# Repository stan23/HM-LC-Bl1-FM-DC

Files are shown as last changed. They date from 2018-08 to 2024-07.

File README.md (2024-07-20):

# HM-LC-Bl1-FM-DC          
Nachbau HM-LC-Bl1-FM Rollladenaktor für Gleichstrommotoren (z.B. Plissee)

Er verhält sich wie ein Rolloaktor, treibt aber einen 12/24 V Gleichstrommotor. Dieser wird je nach Fahrtrichtung umgepolt.

Dies basiert auf der hervorragenden Arbeit von [pa-pa](https://github.com/pa-pa/AskSinPP),  [Jérôme](https://github.com/jp112sdl/Beispiel_AskSinPP) und micha68.

[Link zur neueren Version der Platine](https://github.com/stan23/myPCBs/tree/master/HM-LC-Bl1-FM-DC)

## Hardware

### Bauteile

#### Reichelt

[Bestellliste](https://www.reichelt.de/my/1495010)

Bauteil                  | Bestellnummer   | Anzahl | Kommentar
------------------------ | --------------- | ------ | ---------
C6                       | X5R-G0603 10/6  |   1    | -
C1, C2, C3, C8, C21, C22 | X7R-G0603 100N  |   6    | -
C7                       | TAJ 3528 3,3/35 |   1    |  -
R22, R24                 | RND 0603 1 47   |   1    | -
R2                       | RND 0603 1 1,5K |   2    | -
R11, R12                 | RND 0603 1 2,7K |   2    | -
R1, R21, R23             | RND 0603 1 10K  |   3    | -
D1                       | SLO SMD-Y0603-0 |   1    | -
D2, D11, D12             | 1N 4148 WS      |   3    | -
Q1, Q2                   | BC 817 NXP      |   2    | -
U1                       | ATMEGA 328P-AU  |   1    | -
U3                       | SIM1-2403 SIL4  |   1    | für 24 V
U3                       | SIM1-1203 SIL4  |   1    | alternativ für 12 V
K1, K2                   | G6S-2 24V       |   2    | für 24 V
K1, K2                   | G6S-2 12V       |   2    | alternativ für 12 V
X1                       | WAGO 250-204    |   1    | -
X2                       | WAGO 250-404    |   1    | siehe [Issue #1](https://github.com/stan23/HM-LC-Bl1-FM-DC/issues/1)
Verbinder zu U2          | SL 1X20G 2,00   |   1    | -
Verbinder zu U2          | MPE 156-1-032   |   1    | optional

#### Sonstiges

Bauteil | Bestellnummer            | Anzahl | Kommentar
------- | ------------------------ | ------ | ---------
U2      | CC1101 Funkmodul 868MHz  |   1    | z.B. [eBay](https://www.ebay.de/itm/272455136087)

### Programmieradapter
- 1x ISP (um den Bootloader zu brennen)
- 1x FTDI Adapter (falls nicht schon vorhanden, gibts bei [Amazon](https://www.amazon.de/FT232RL-FTDI-USB-auf-TTL-Serienadapter-Arduino/dp/B00HSXDGOE))

## Software

### Fuses

Low:  0xE2
High: 0xD2
Ext:  0xFF

### Bootloader

Aus der Arduino IDE, für ATmega328P, 3,3 V, 8 MHz

### Firmware

https://github.com/pa-pa/AskSinPP/tree/master/examples/HM-LC-Bl1-FM

## Bilder

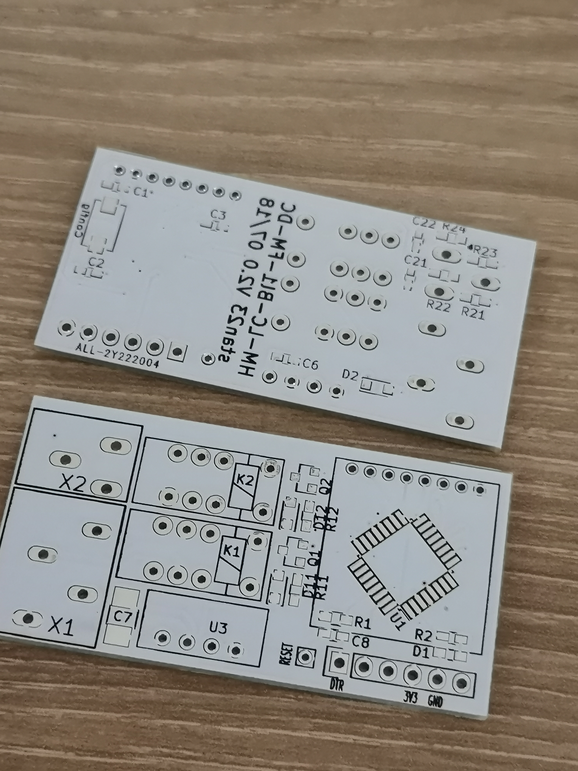
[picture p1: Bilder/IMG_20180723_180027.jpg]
nackte Platine

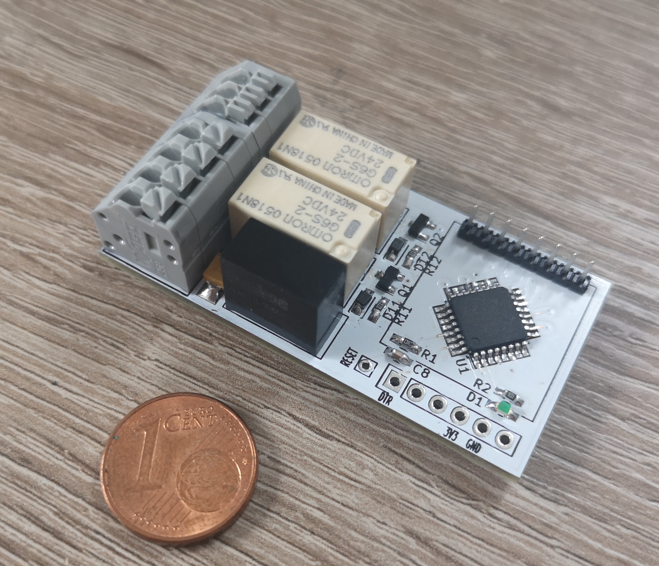
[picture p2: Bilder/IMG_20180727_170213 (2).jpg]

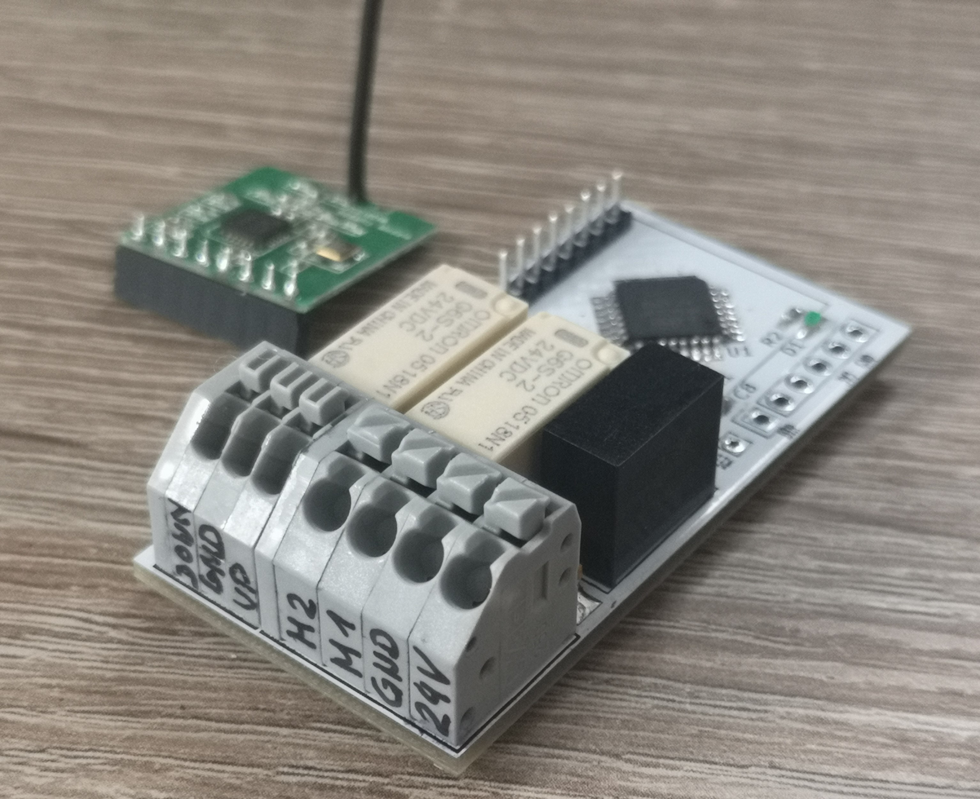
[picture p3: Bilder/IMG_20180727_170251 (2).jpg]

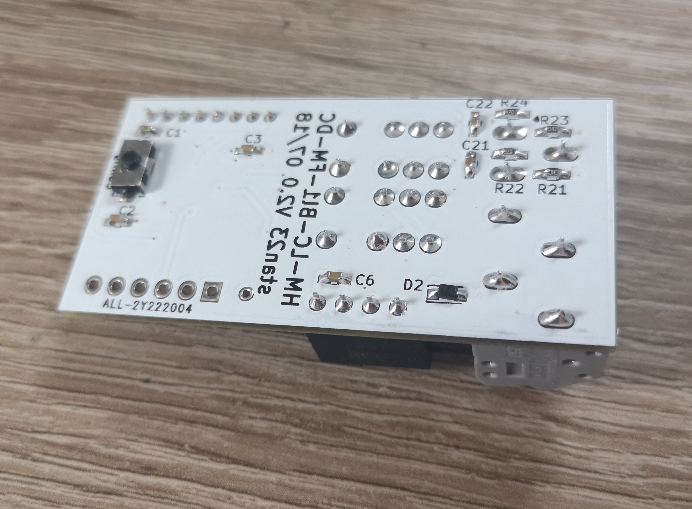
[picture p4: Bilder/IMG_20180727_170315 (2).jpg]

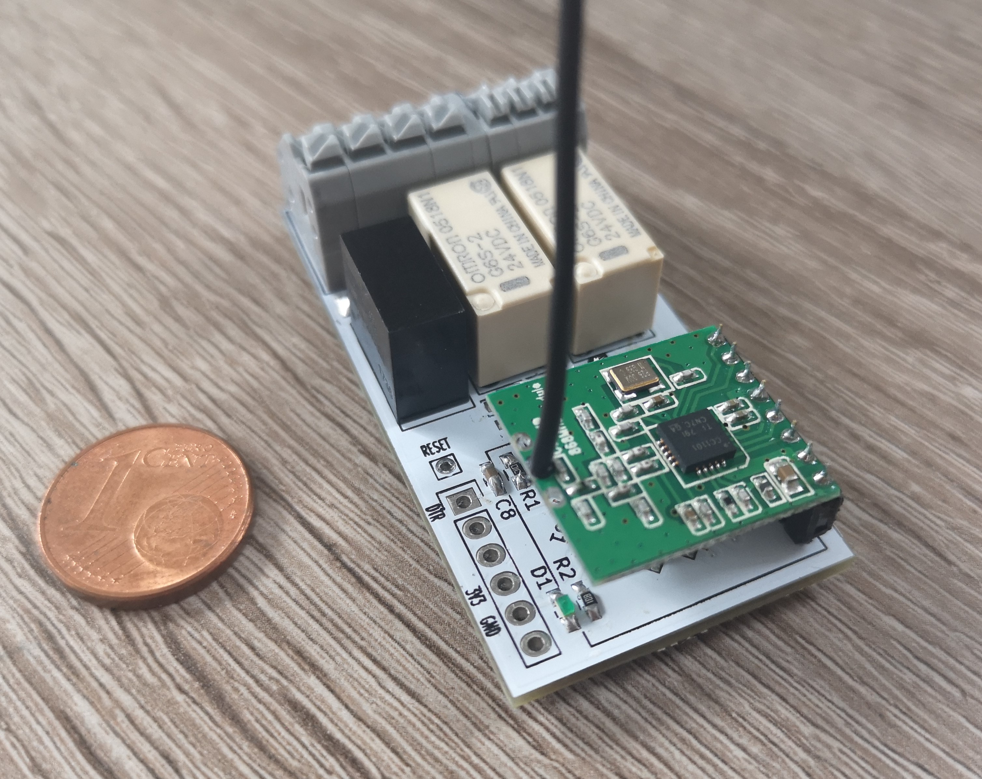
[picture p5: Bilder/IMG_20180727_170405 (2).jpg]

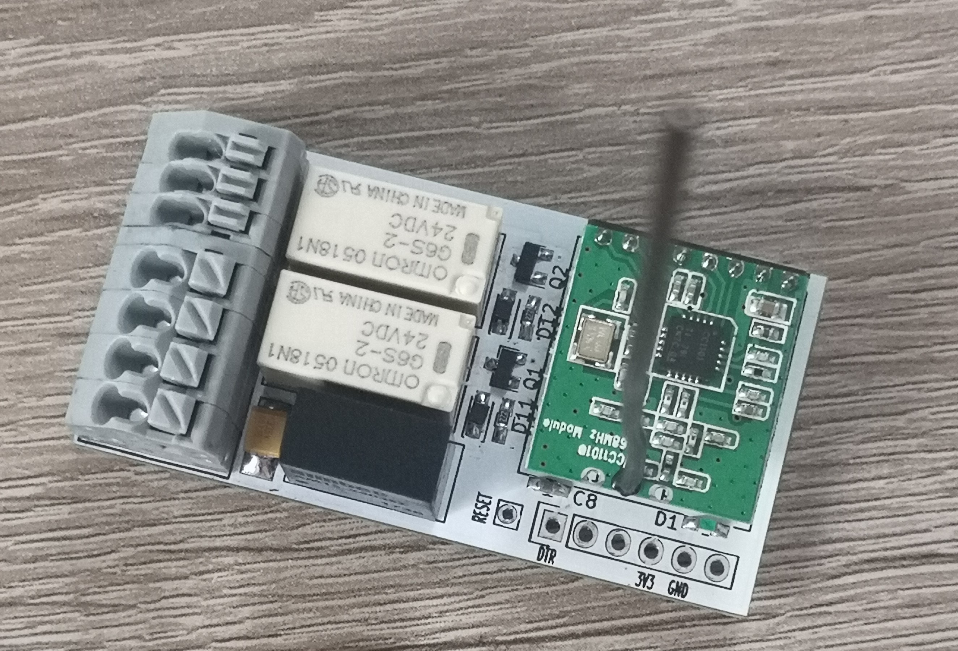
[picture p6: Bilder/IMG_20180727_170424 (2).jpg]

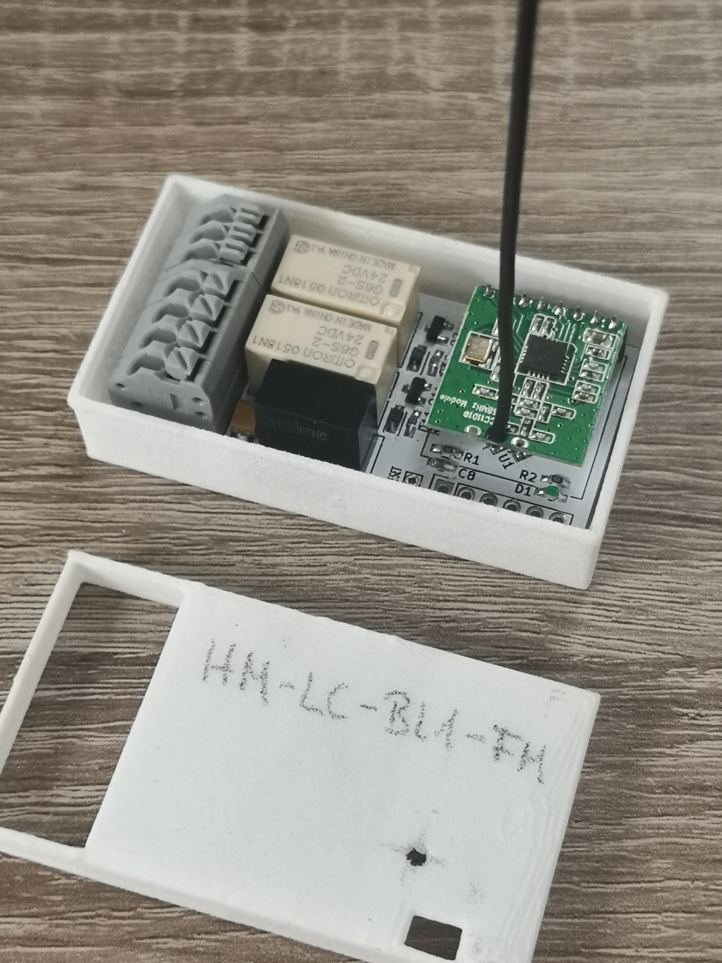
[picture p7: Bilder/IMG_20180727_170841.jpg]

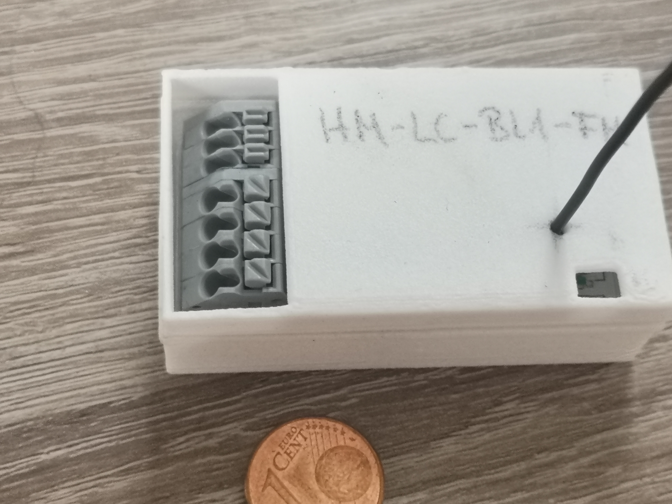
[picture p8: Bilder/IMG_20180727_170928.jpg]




Dieses Werk ist lizenziert unter einer [Creative Commons Namensnennung - Nicht-kommerziell - Weitergabe unter gleichen Bedingungen 4.0 International Lizenz](http://creativecommons.org/licenses/by-nc-sa/4.0/).

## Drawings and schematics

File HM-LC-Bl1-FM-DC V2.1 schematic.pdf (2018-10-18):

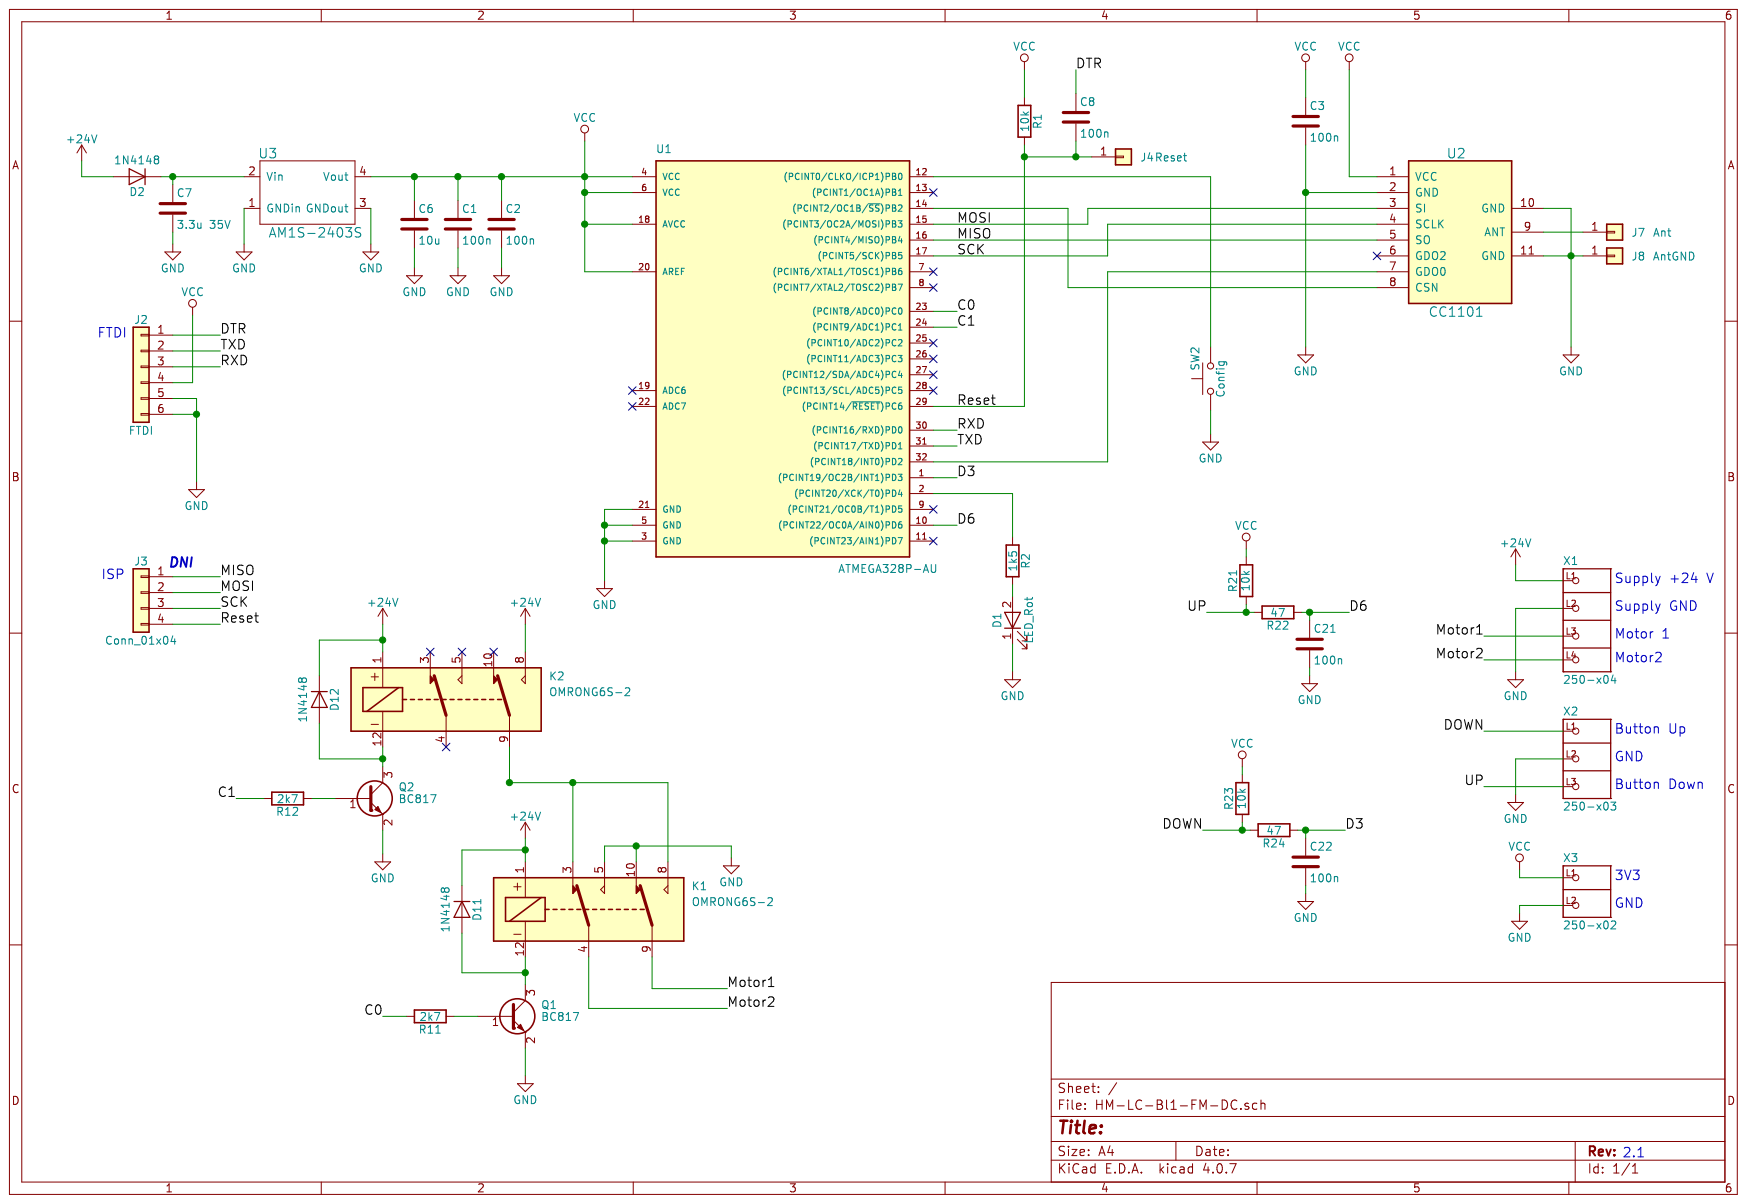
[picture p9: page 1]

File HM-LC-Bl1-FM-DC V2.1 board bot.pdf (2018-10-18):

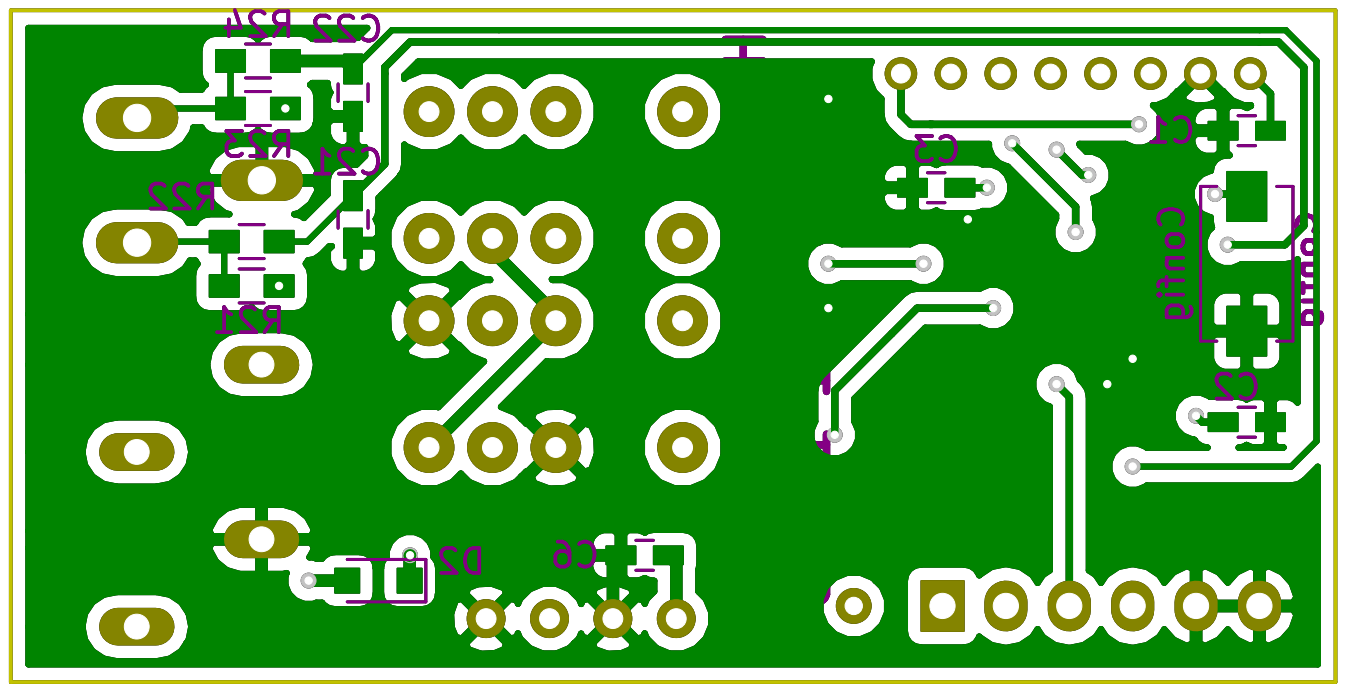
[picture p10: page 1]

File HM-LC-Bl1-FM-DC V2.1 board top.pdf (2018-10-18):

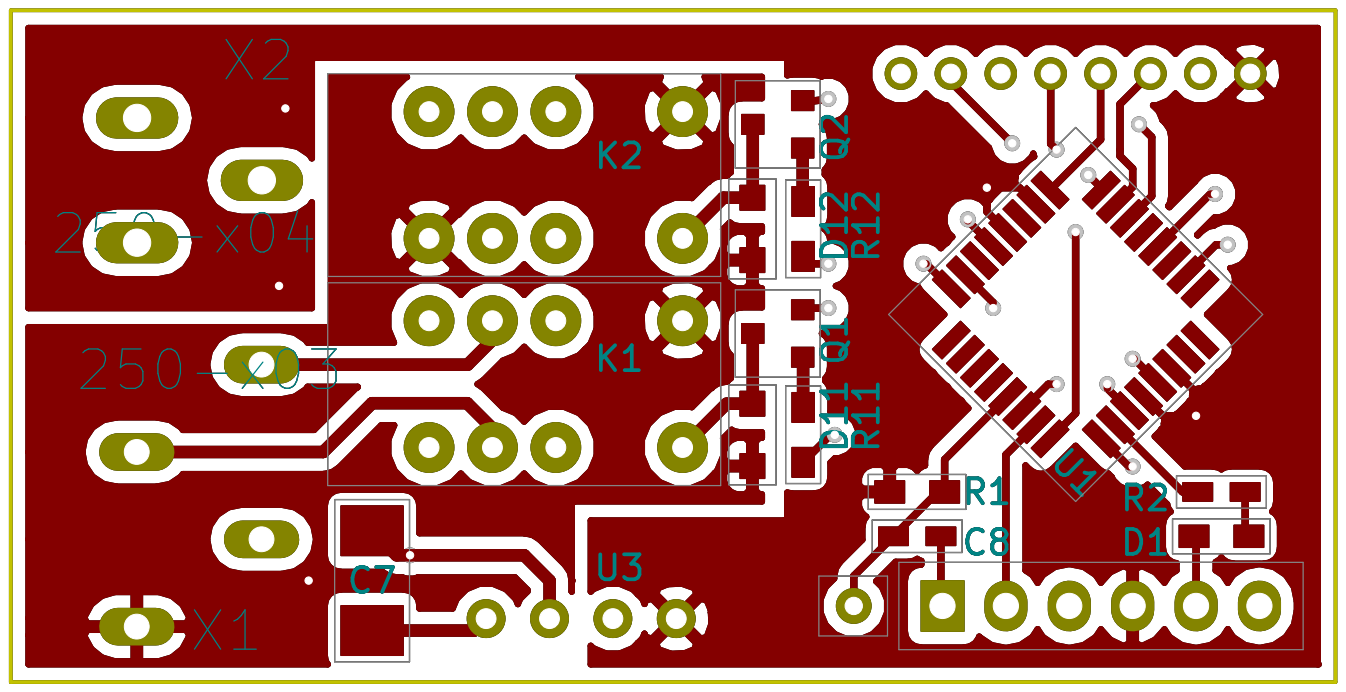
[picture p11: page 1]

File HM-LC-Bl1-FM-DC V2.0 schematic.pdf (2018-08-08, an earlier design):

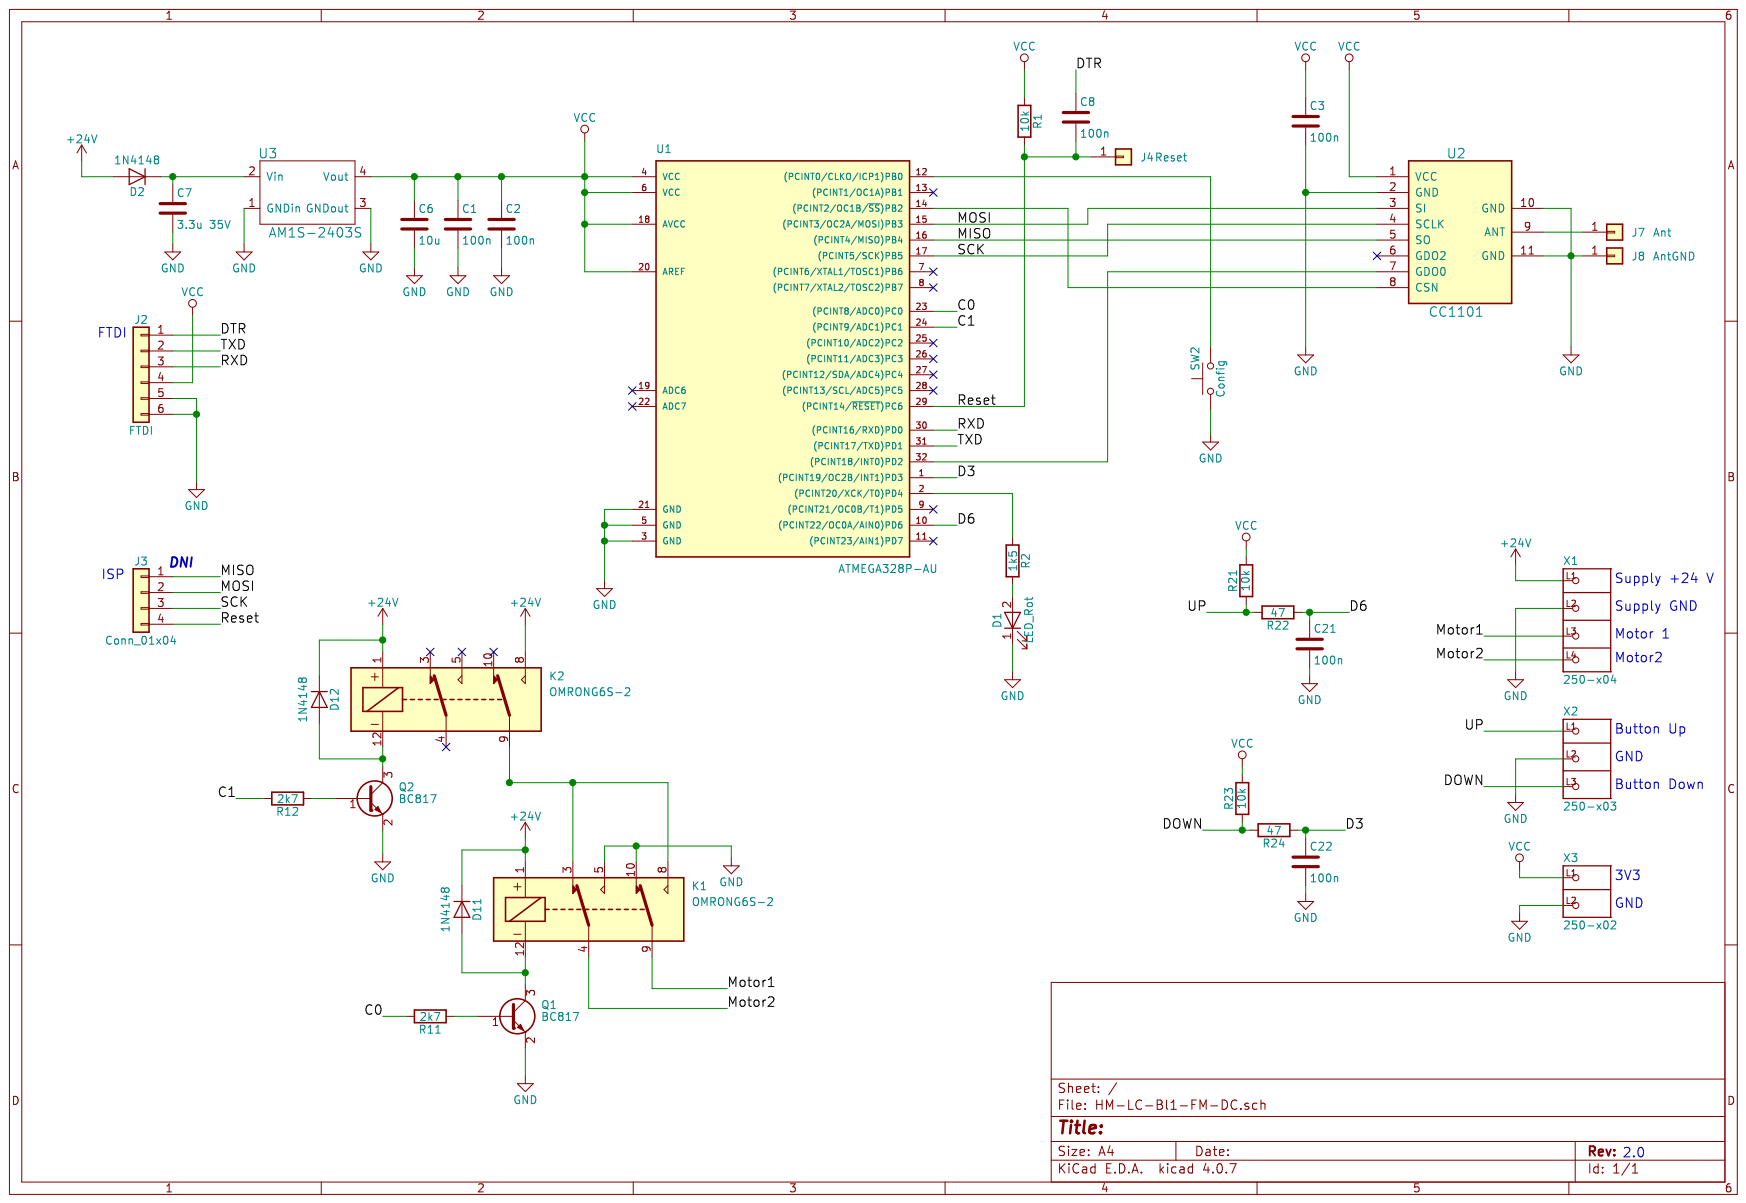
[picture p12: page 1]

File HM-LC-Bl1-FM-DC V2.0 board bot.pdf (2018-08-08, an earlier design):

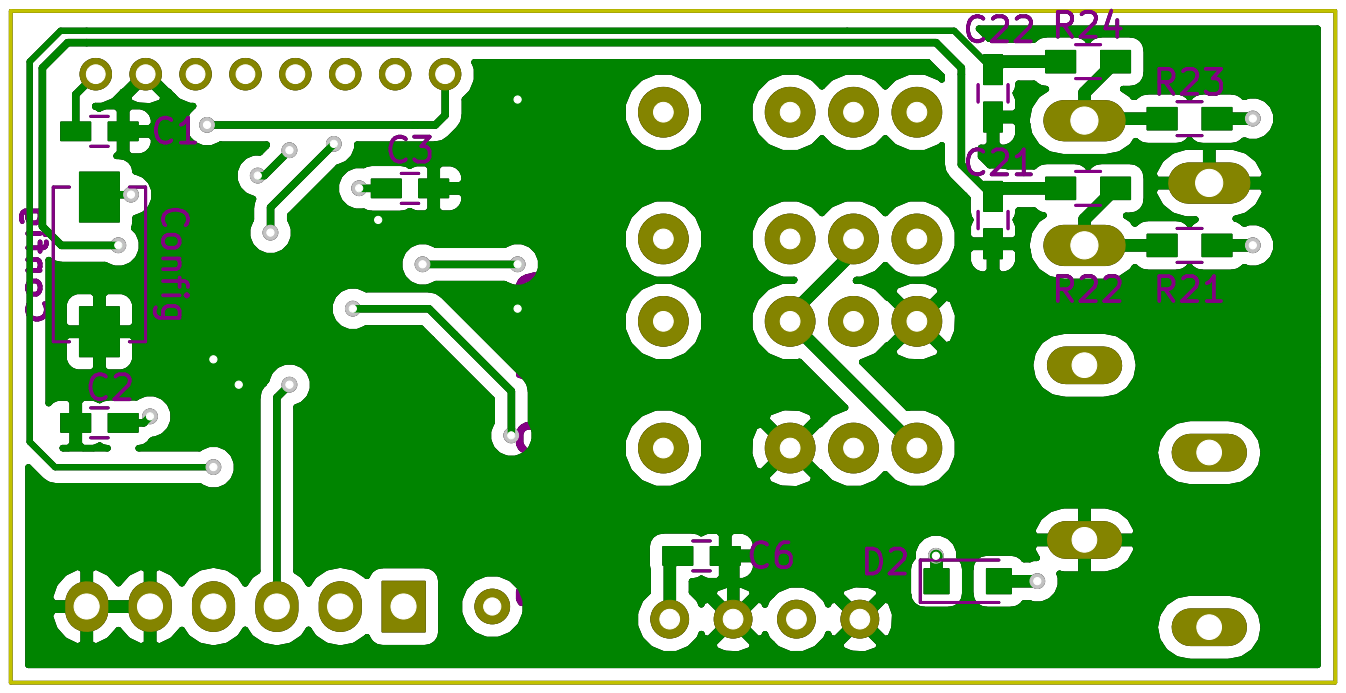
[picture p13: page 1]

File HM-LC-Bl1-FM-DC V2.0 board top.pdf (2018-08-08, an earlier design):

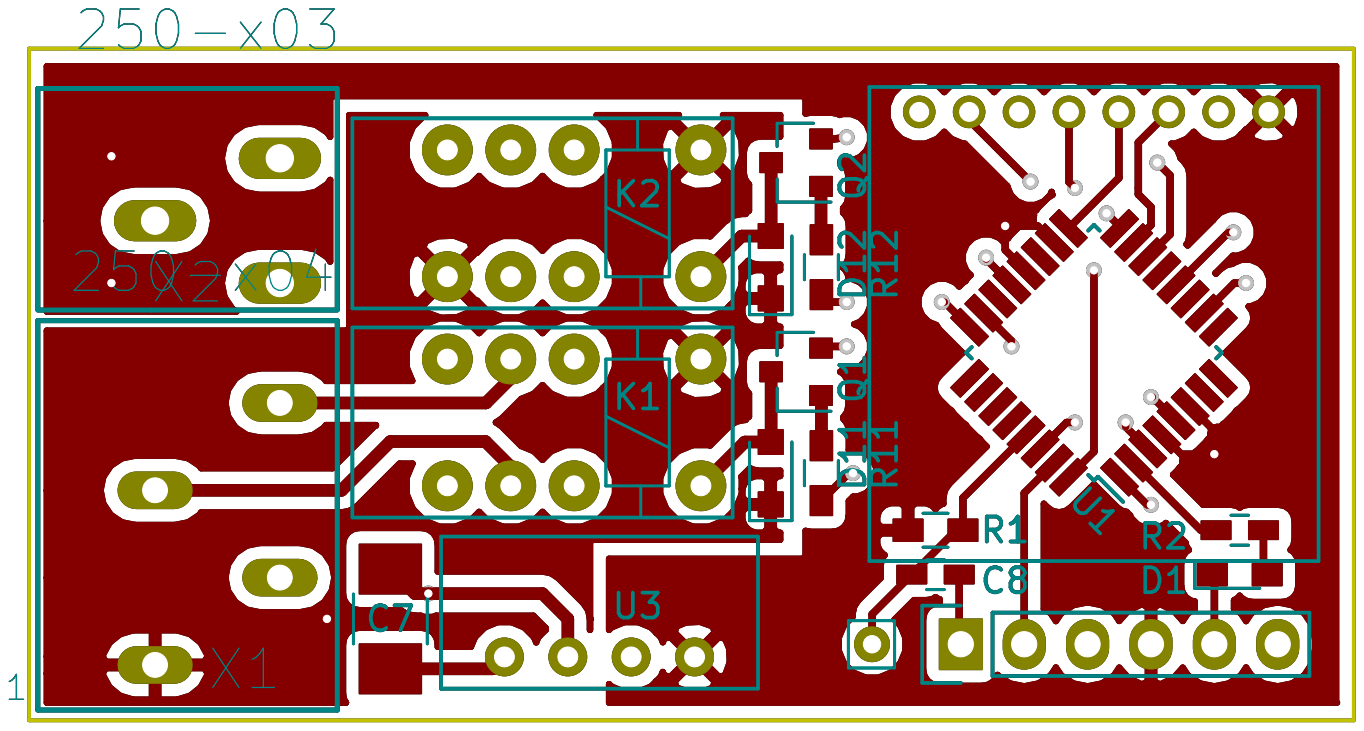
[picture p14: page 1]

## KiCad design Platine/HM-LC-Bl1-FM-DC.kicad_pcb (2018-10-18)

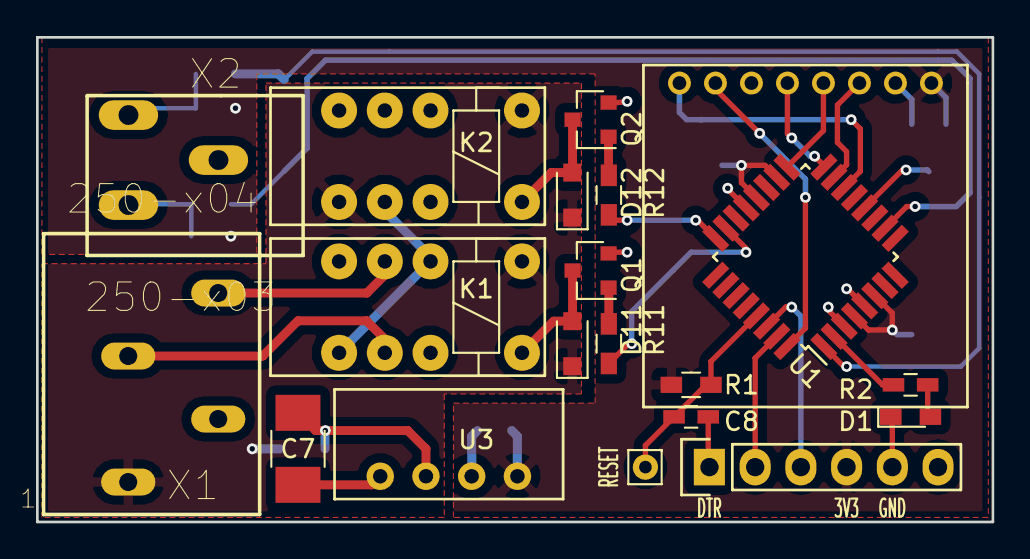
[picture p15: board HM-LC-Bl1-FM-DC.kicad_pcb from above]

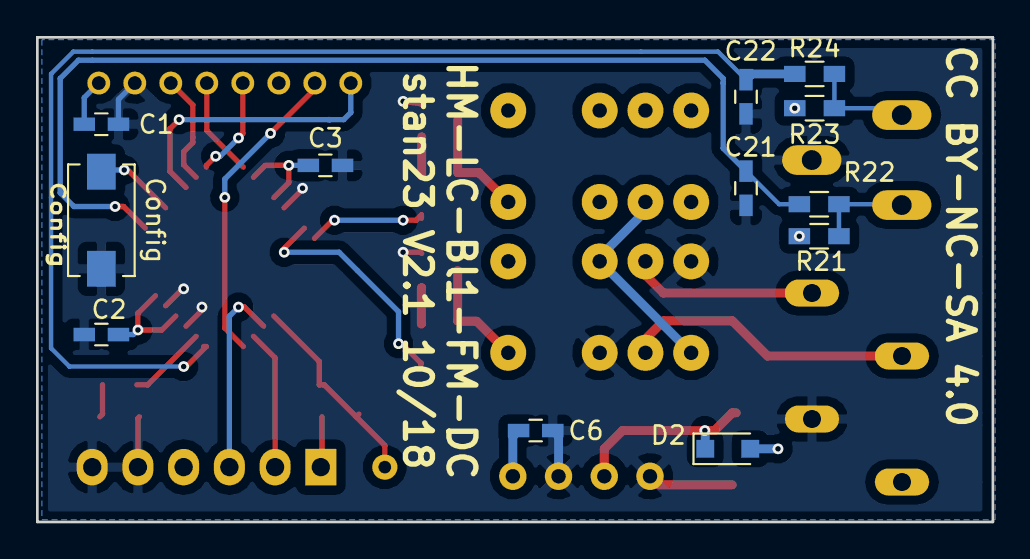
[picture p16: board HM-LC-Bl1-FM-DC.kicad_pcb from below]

Board: 2 copper layers, 53.1 x 26.9 mm, 32 parts (12 on the bottom side), 29 nets.

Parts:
C1, C2, C3, C8, C21, C22: 100n; C_0603_HandSoldering
C6: 10u; C_0603_HandSoldering
C7: 3.3u 35V; C_1210_HandSoldering
D1: LED_Rot; LED_0603_HandSoldering
D2, D11, D12: 1N4148; D_SOD-323_HandSoldering
J2: FTDI; Pin_Header_Straight_1x06
J4: Reset; Pin_d0.7mm_L6.5mm_W1.8mm_FlatFork
K1, K2: OMRONG6S-2; Relay_Omron_G6S-2
Q1, Q2: BC817; SOT-23
R1, R21, R23: 10k; R_0603_HandSoldering
R2: 1k5; C_0603_HandSoldering
R11, R12: 2k7; R_0603_HandSoldering
R22, R24: 47; R_0603_HandSoldering
SW2: Config; SW_SPST_EVQPE1
U1: ATMEGA328P-AU; TQFP-32_7x7mm_Pitch0.8mm
U2: CC1101; CC1101_Module
U3: AM1S-2403S; SIL-4
X1: 250-x04; P-250-204
X2: 250-x03; P-250-403

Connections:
+24V: D2.2, D11.1, D12.1, K1.1, K2.1, K2.8, X1.L1
/C0: R11.2, U1.23
/C1: R12.2, U1.24
/D3: C22.1, R24.1, U1.1
/D6: C21.1, R22.1, U1.10
/DOWN: R23.1, R24.2, X2.L1
/DTR: C8.1, J2.1
/MISO: U1.16, U2.5
/MOSI: U1.15, U2.3
/Motor1: K1.9, X1.L3
/Motor2: K1.4, X1.L4
/RXD: J2.3, U1.30
/Reset: C8.2, J4.1, R1.2, U1.29
/SCK: U1.17, U2.4
/TXD: J2.2, U1.31
/UP: R21.1, R22.2, X2.L3
GND: C1.2, C2.2, C3.2, C6.2, C7.2, C21.2, C22.2, D1.1, J2.5, J2.6, K1.5, K1.10, Q1.2, Q2.2, SW2.1, U1.3, U1.5, U1.21, U2.2, U3.1, U3.3, X1.L2, X2.L2
unnamed: C7.1, D2.1, U3.2
unnamed: D1.2, R2.2
unnamed: D11.2, K1.12, Q1.3
unnamed: D12.2, K2.12, Q2.3
unnamed: K1.3, K1.8, K2.9
unnamed: Q1.1, R11.1
unnamed: Q2.1, R12.1
unnamed: R2.1, U1.2
unnamed: SW2.2, U1.12
unnamed: U1.14, U2.8
unnamed: U1.32, U2.7
VCC: C1.1, C2.1, C3.1, C6.1, J2.4, R1.1, R21.2, R23.2, U1.4, U1.6, U1.18, U1.20, U2.1, U3.4

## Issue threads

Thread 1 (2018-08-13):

V2.0: X2 (WAGO 250-40x) hat falschen Footprint

stan23, 2018-08-13:
Platine V2.0
Der Footprint von X2 (WAGO 250-403) ist spiegelverkehrt.

Workaround:
WAGO 250-404 bestellen und eine Klemme ausbauen.

stan23, 2018-10-18:
fixed in V2.1

stan23, 2018-10-31:
Still not fixed :flushed:

stan23, 2024-02-11:
fixed in version 3:
https://github.com/stan23/myPCBs/tree/master/HM-LC-Bl1-FM-DC

Closed 2024-02-11.

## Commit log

2018-08-08 add KiCad files
    [HM-LC-Bl1-FM-DC.kicad_pcb, HM-LC-Bl1-FM-DC.sch]
2018-08-08 update schematic to include the values
2018-10-18 update to 2.1
    fix mirrored footprint of X2
    [HM-LC-Bl1-FM-DC.kicad_pcb, HM-LC-Bl1-FM-DC.sch]
2019-07-22 alternate placement for 12 V supply

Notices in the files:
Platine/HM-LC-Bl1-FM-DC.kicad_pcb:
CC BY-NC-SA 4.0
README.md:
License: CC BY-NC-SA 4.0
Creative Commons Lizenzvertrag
